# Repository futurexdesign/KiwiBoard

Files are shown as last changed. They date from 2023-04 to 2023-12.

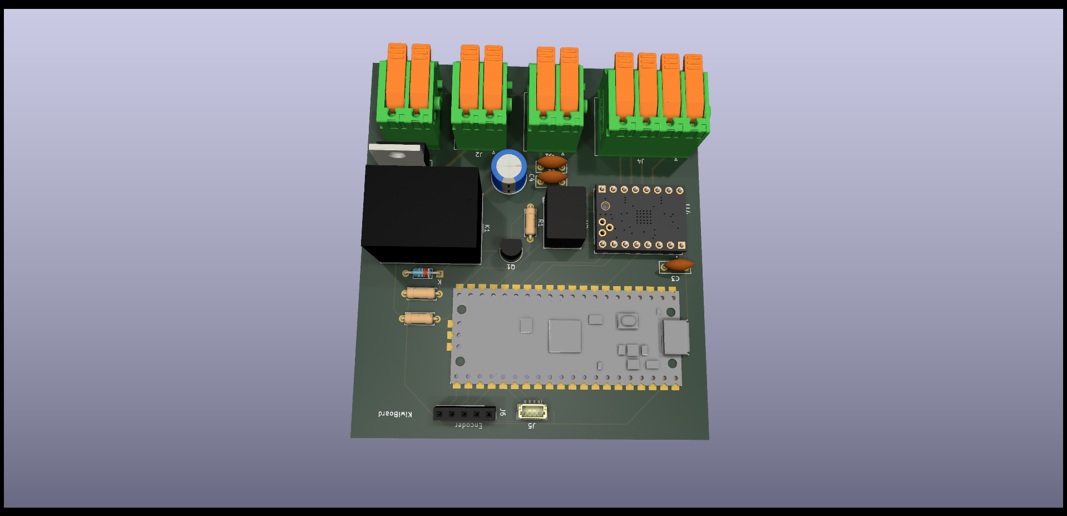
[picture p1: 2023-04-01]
Screenshots/KiwiBoard2.png

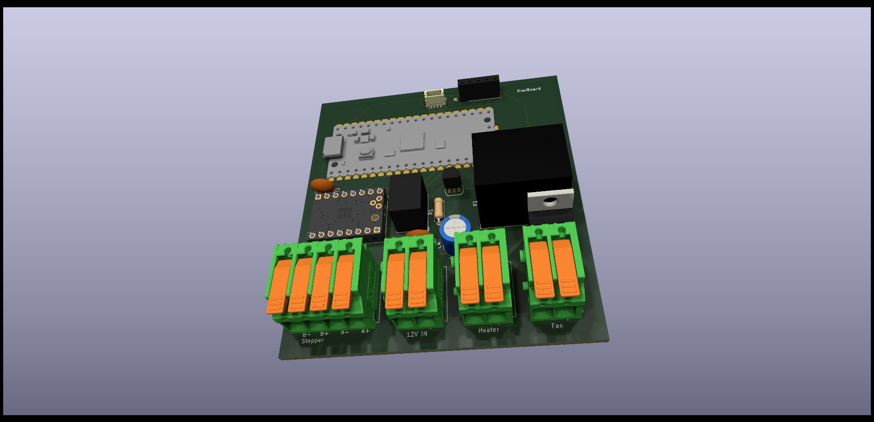
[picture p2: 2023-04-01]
Screenshots/KiwiBoard.png

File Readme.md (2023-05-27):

# Kiwiboard 
Control board for the KiwiCleaner watch cleaning machine.  Intended to provide an all-in-one option for the design. 

## Board Goals
- Have a single PCB with connections for the stepper motor, heater, fan, and user interface for ease of wiring. 
- Integrate a Trinamic silent stepper driver to greatly reduce volume. 
- Simplify the user interface for switching between run-modes. 
- Allow cooling fan to run for a timed period after a dry cycle, to allow the heater to safely cool down. 
- Not cost too much more than the original solution, with the understanding that there is greater functionality. 

## Theory of Operation
- Power input is 12V 
- Input is protected by a resettable PolyFuse with rated 10A constant load capacity.  
- Main Microcontroller is a RaspberryPi Pico (RP2040).  
  - This can be either the normal version, or the "header" version.  Can be mounted either way, board contains both the SMD and THT pads. 
- Display a 240x320 Color TFT LCD Connected via SPI
- User interface is controlled via a rotary encoder with pushbutton
- Pico has full control of stepper via SPI connection to the TMC5160 board. 
   - The Integrated Ramp Generator contained within the TMC5160 is utilized to control all motion, allowing very smooth and precise control over basket motion.  
- Pico can enable / disable the drive output via MOTOR_EN (Active Low)
- Pico can activate the Heater by pulling HEATER_CTL High, switching on the relay (3.3v coil).
- Pico can activate the fan by pulling FAN_CTL high, fan current conducted by the TIP120
- 3.3v power provided by a drop in switching powersupply module for simplicity. 
- All power connectors are Phoenix LPT lever connectors.  These support 12awg - 24awg up to a max of 24A.  Can substitute in SPT or any other phoenix connector with the same 5mm pin spacing

An expansion header has been added to support any additional mods people may want. *Example functionality would be a buzzer module to indicate end of cycle.*  Due to the flexability of the microcontroller, we can expose a ton of functionality on 4 pins.  The following IO is available on the expansion connector. 

- 4 independent GPIO pins for input/output 
- 1 hardware i2c bus (i2c1), and 2 GPIO pins (GPI0 and GPIO1)
- 4 pins with a PIO program assigned to them. 

Additionally the expansion header supplys 3.3V and GND connections.

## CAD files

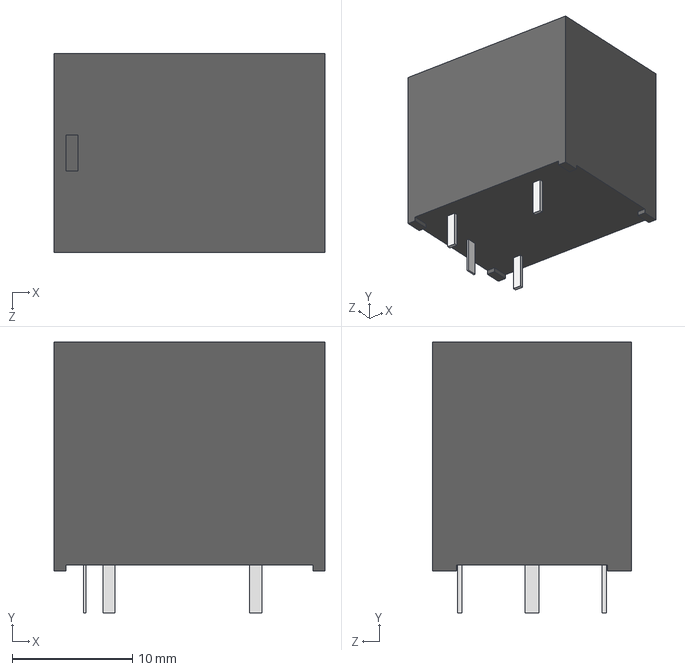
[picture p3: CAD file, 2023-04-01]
project_library/3dmodel/G5LE-1A-EDC5.step
22.5 x 22.5 x 16.5 mm

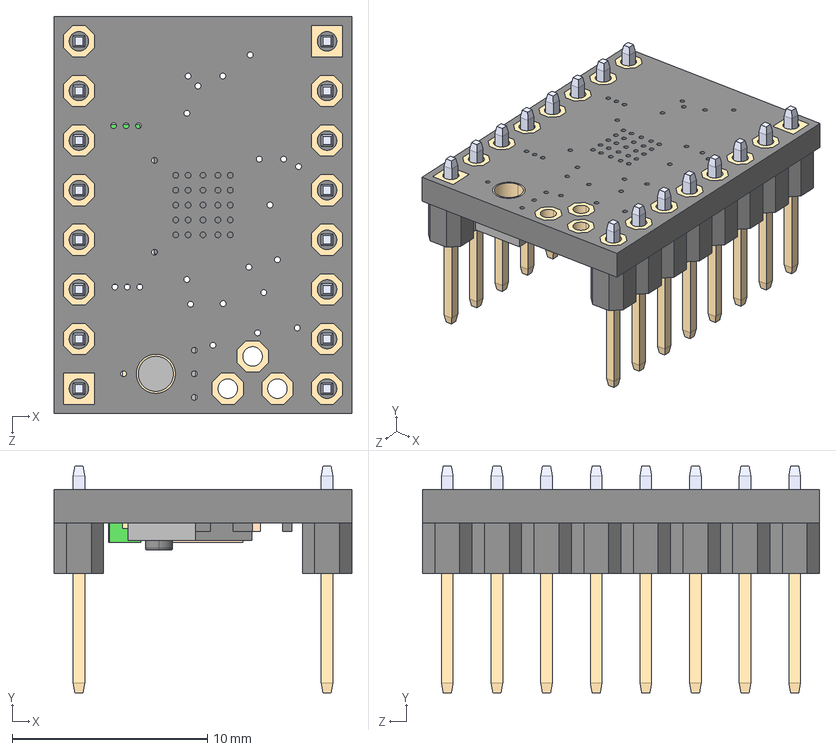
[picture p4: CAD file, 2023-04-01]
project_library/3dmodel/TMC2208_SILENTSTEPSTICK.step
15.2 x 11.6 x 20.3 mm

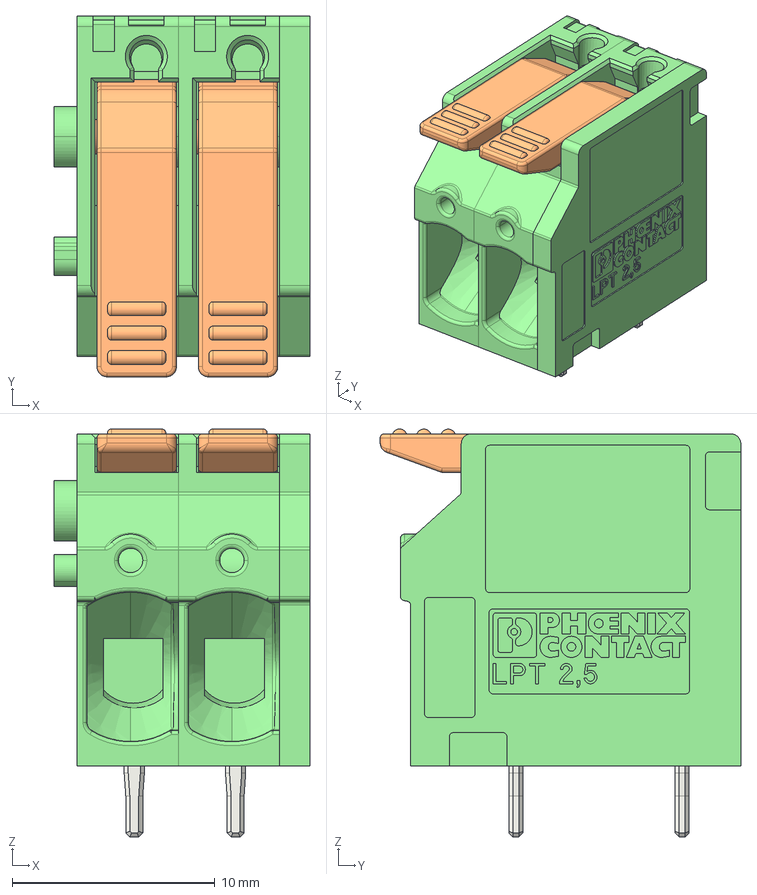
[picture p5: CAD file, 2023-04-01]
project_library/3dmodel/pxc_1190297_02_LPT-2-5-2-5-0_3D.stp
12.6 x 17.8 x 20.1 mm
LP_LPT_2_5_3_50.2.2 x 4
AC_LPT_2_5_LEVER x 2
PK_LPT_2_5_5_00 x 2
DK_LPT_2_5_5_00

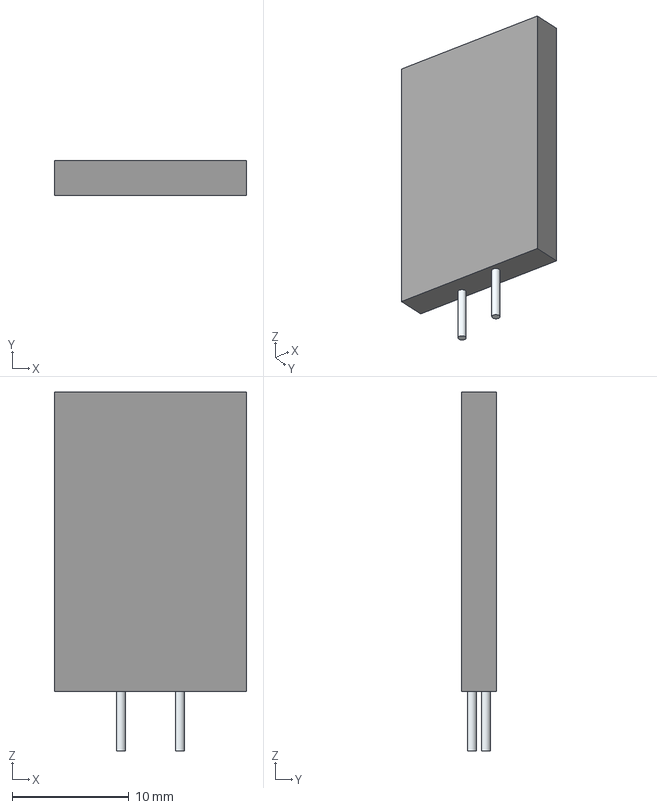
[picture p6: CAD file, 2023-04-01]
project_library/3dmodel/AGRF1000.stp
16.5 x 3.00 x 30.8 mm
Leads

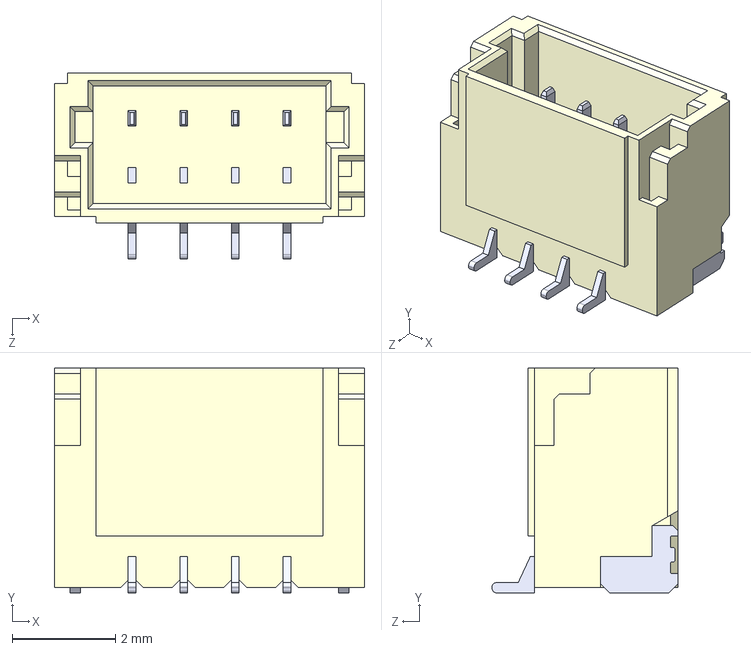
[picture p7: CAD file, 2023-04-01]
project_library/3dmodel/BM04B-SRSS-TBT_LF__SN_.step
6.00 x 4.35 x 3.60 mm

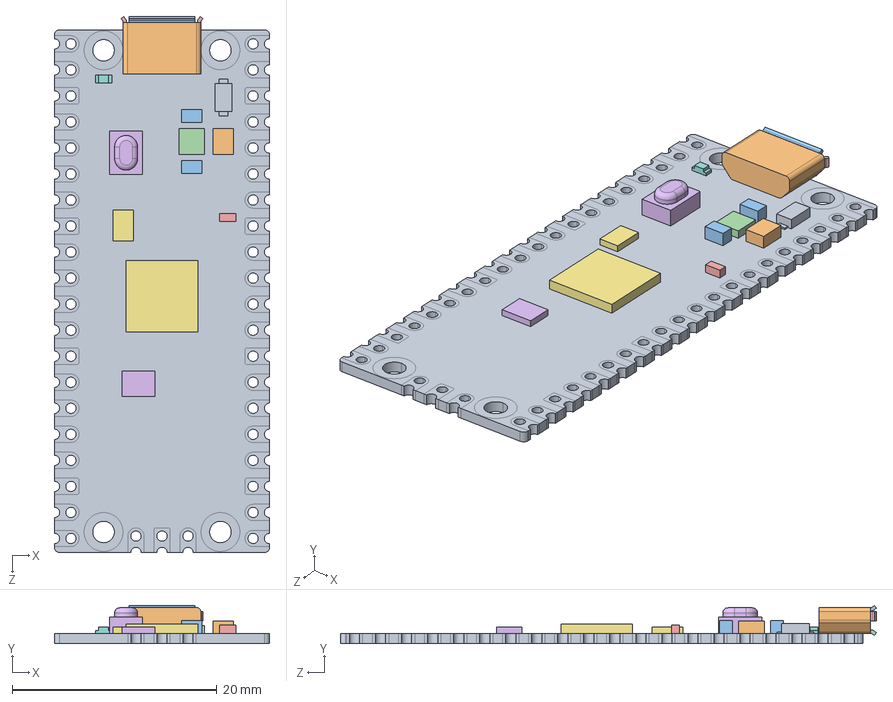
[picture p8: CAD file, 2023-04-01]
project_library/3dmodel/Pico-R3.step
21.0 x 3.73 x 52.3 mm
PICO_REF_BOARD.STEP
PICO_REF_USB.STEP
PICO_REF_SWITCH.STEP
PICO_REF_MICROCONTROLLER.STEP
PICO_REF_LED.STEP
PICO_REF_ONSEMI.STEP
PICO_BOURNS.STEP
PICO_MURATA.STEP x 2
PICO_RICHTEK.STEP
PICO_DIODES.STEP
PICO_AEL.STEP
PICO_WINBOND.STEP

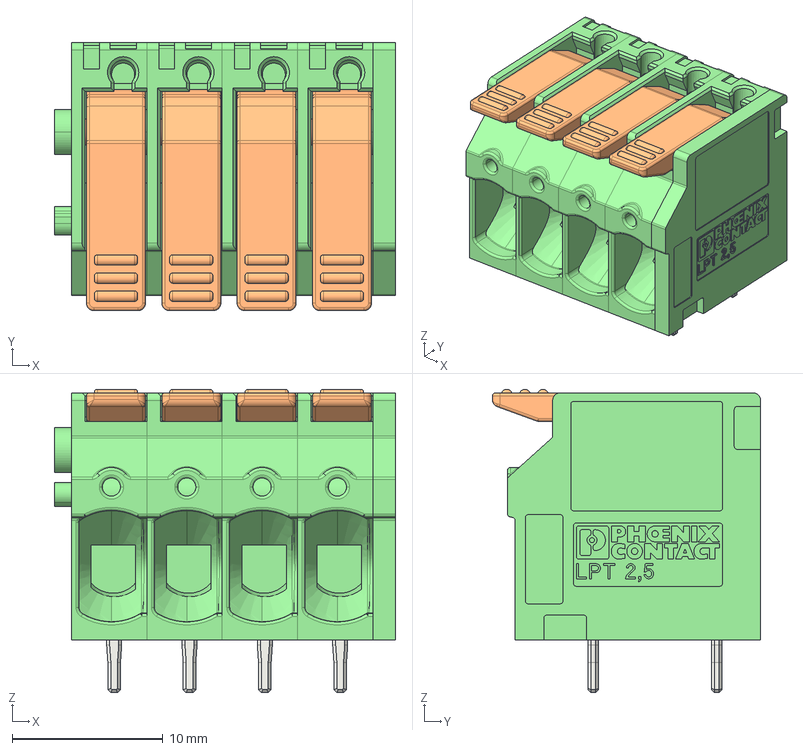
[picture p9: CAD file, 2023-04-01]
project_library/3dmodel/pxc_1190299_02_LPT-2-5-4-5-0_3D.stp
22.6 x 17.8 x 20.1 mm
LP_LPT_2_5_3_50.4 x 8
PK_LPT_2_5_5_00.2 x 4
AC_LPT_2_5_LEVER.2 x 4
DK_LPT_2_5_5_00

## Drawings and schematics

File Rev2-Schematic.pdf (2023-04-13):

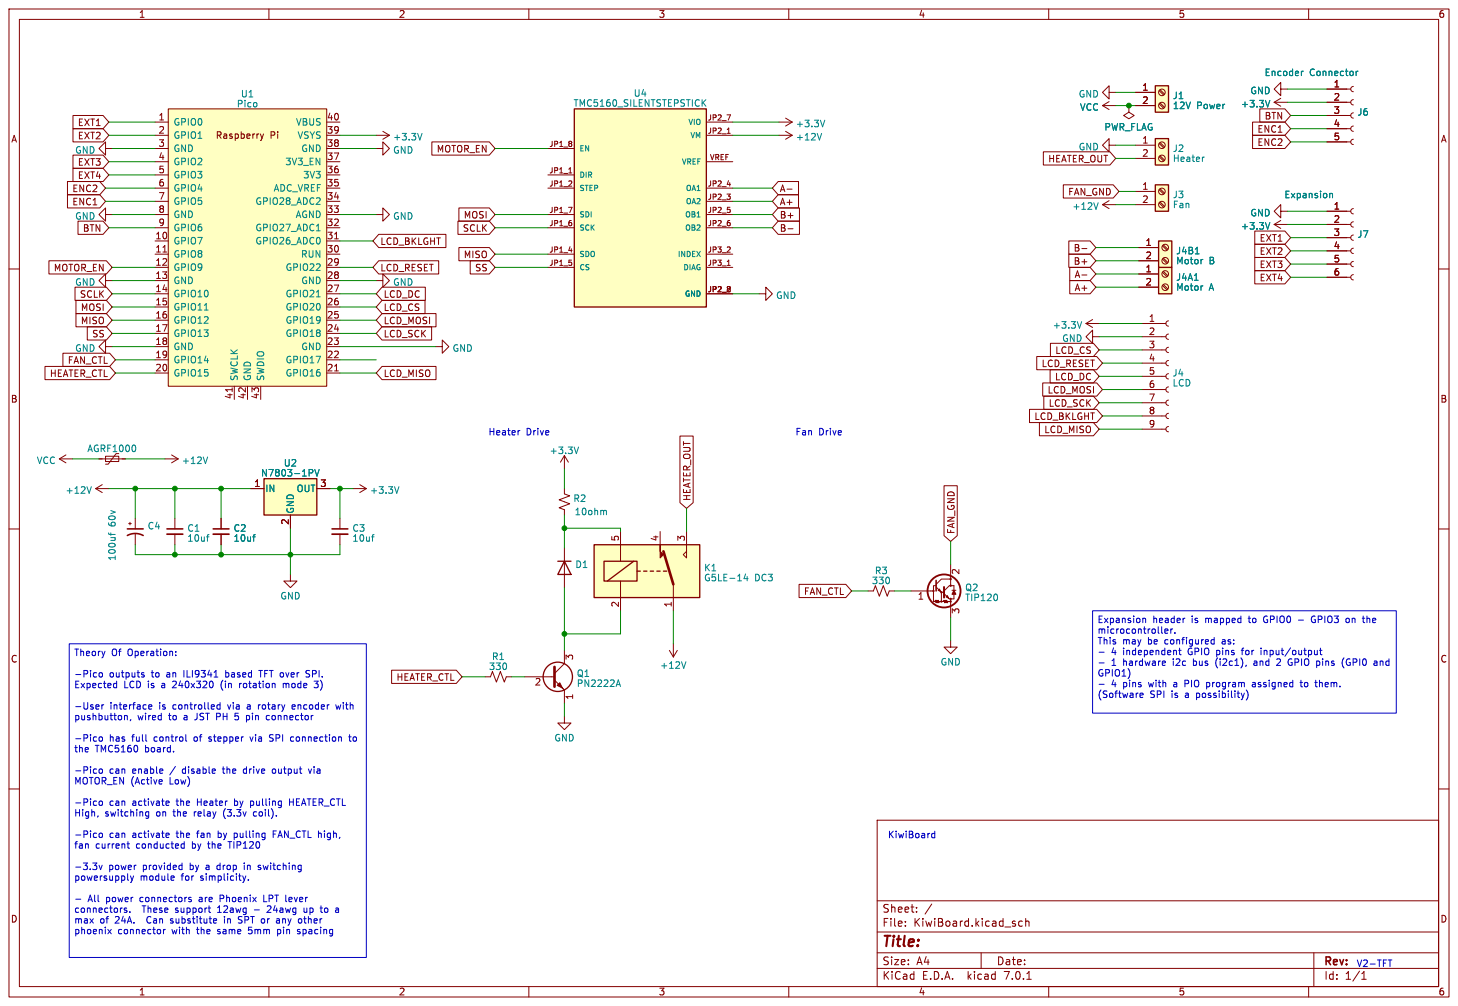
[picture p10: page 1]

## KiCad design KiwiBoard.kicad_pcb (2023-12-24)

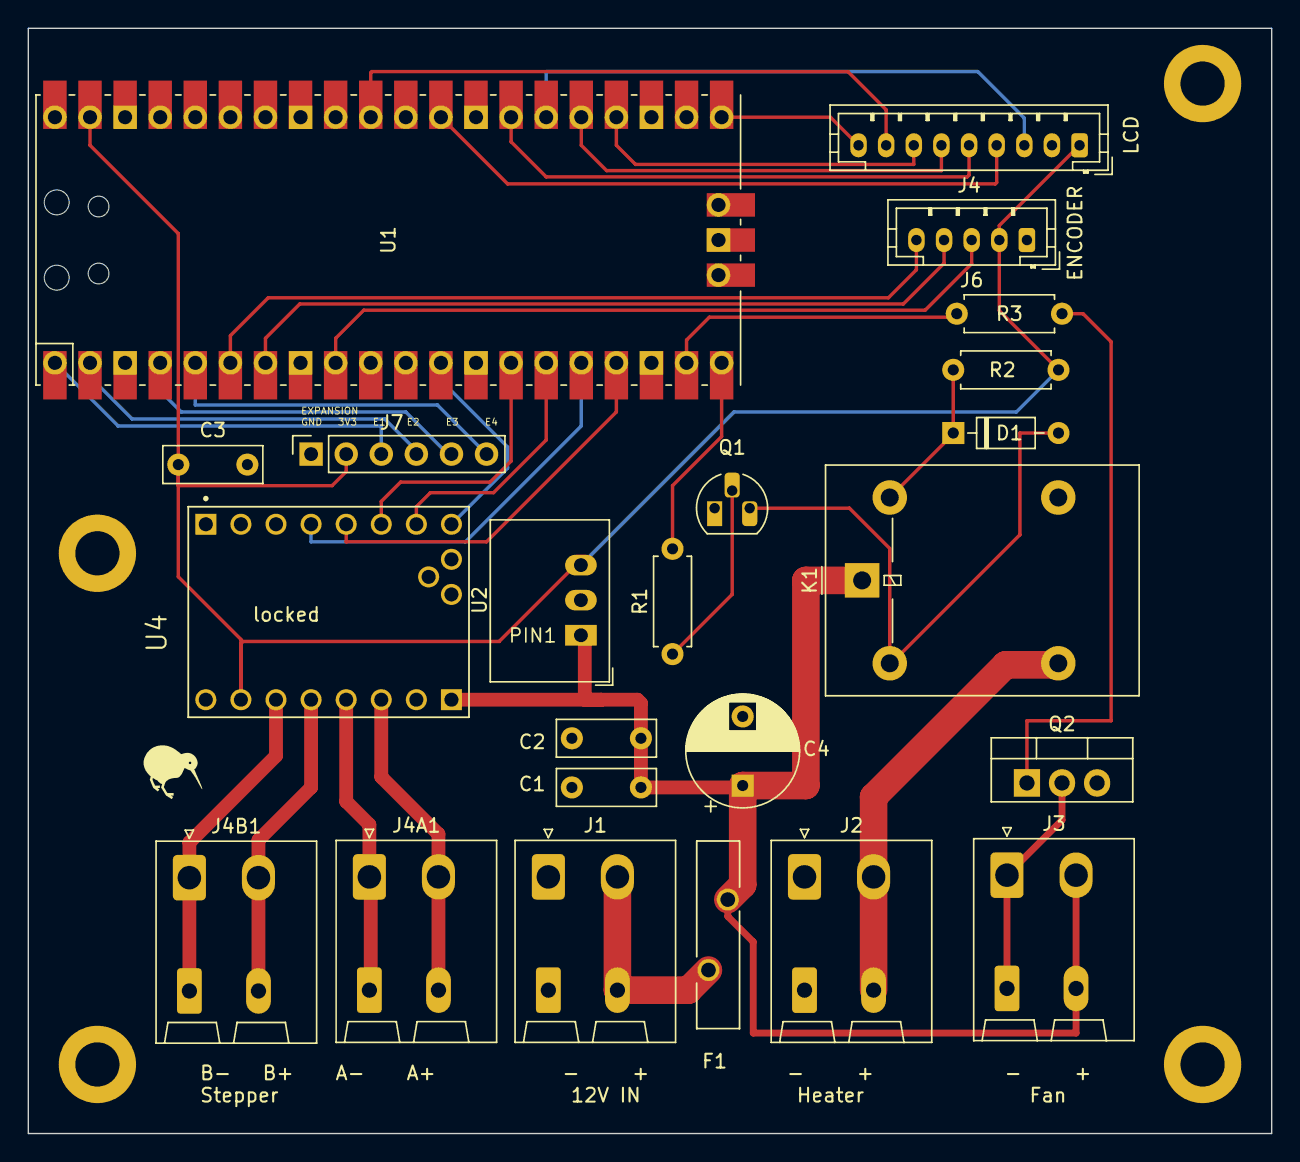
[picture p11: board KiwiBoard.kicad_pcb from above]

Board: 2 copper layers, 90.0 x 80.0 mm, 23 parts (0 on the bottom side), 35 nets.

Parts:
C1, C2, C3: 10uf; C_Disc_D7.0mm_W2.5mm_P5.00mm
C4: 100uf 60v; CP_Radial_D8.0mm_P5.00mm
D1: 1N4148; D_DO-35_SOD27_P7.62mm_Horizontal
F1: AGRF1000; FUSRB510W81L1358T310H1980
J1: 12V Power; Kiwiboard - PhoenixContact_SPT_2.5_2-H-5.0-EX_1x02_P5.0mm_H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
J2: Heater; Kiwiboard - PhoenixContact_SPT_2.5_2-H-5.0-EX_1x02_P5.0mm_H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
J3: Fan; Kiwiboard - PhoenixContact_SPT_2.5_2-H-5.0-EX_1x02_P5.0mm_H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
J4: LCD; JST_PH_B9B-PH-K_1x09_P2.00mm_Vertical
J4A1: Motor A; Kiwiboard - PhoenixContact_SPT_2.5_2-H-5.0-EX_1x02_P5.0mm_H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
J4B1: Motor B; Kiwiboard - PhoenixContact_SPT_2.5_2-H-5.0-EX_1x02_P5.0mm_H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
J6: Encoder Connector; JST_PH_B5B-PH-K_1x05_P2.00mm_Vertical
J7: Expansion; PinSocket_1x06_P2.54mm_Vertical
K1: G5LE-14 DC3; Relay_SPDT_Omron-G5LE-1
Q1: PN2222A; TO-92_HandSolder
Q2: TIP120; TO-220-3_Vertical
R1, R3: 330; R_Axial_DIN0207_L6.3mm_D2.5mm_P7.62mm_Horizontal
R2: 10OHM-1/10W-5%; R_Axial_DIN0207_L6.3mm_D2.5mm_P7.62mm_Horizontal
U1: Pico; RPi_Pico_SMD_TH
U2: N7803-1PV; Converter_DCDC_RECOM_R-78E-0.5_THT
U4: TMC5160_SILENTSTEPSTICK; MODULE_TMC2208_SILENTSTEPSTICK

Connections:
+3.3V: C3.1, J4.1, J6.2, J7.2, R2.1, U1.39 (VSYS), U2.3 (OUT), U4.JP2_7 (VIO)
+12V: C1.1, C2.1, C4.1, F1.2, J3.2, K1.1, U2.1 (IN), U4.JP2_1 (VM)
A+: J4A1.2, U4.JP2_3 (OA2)
A-: J4A1.1, U4.JP2_4 (OA1)
B+: J4B1.2, U4.JP2_5 (OB1)
B-: J4B1.1, U4.JP2_6 (OB2)
BTN: J6.3, U1.9 (GPIO6)
ENC1: J6.4, U1.7 (GPIO5)
ENC2: J6.5, U1.6 (GPIO4)
EXT1: J7.3, U1.1 (GPIO0)
EXT2: J7.4, U1.2 (GPIO1)
EXT3: J7.5, U1.4 (GPIO2)
EXT4: J7.6, U1.5 (GPIO3)
FAN_CTL: R3.2, U1.19 (GPIO14)
FAN_GND: J3.1, Q2.2 (C)
GND: C1.2, C2.2, C3.2, C4.2, J1.1, J2.1, J4.2, J6.1, J7.1, Q1.1 (E), Q2.3 (E), U1.3 (GND), U1.8 (GND), U1.13 (GND), U1.18 (GND), U1.23 (GND), U1.28 (GND), U1.33 (AGND), U1.38 (GND), U2.2 (GND), U4.JP2_2 (GND), U4.JP2_8 (GND)
HEATER_CTL: R1.2, U1.20 (GPIO15)
HEATER_OUT: J2.2, K1.3
LCD_BKLGHT: J4.8, U1.31 (GPIO26_ADC0)
LCD_CS: J4.3, U1.26 (GPIO20)
LCD_DC: J4.5, U1.27 (GPIO21)
LCD_MISO: J4.9, U1.21 (GPIO16)
LCD_MOSI: J4.6, U1.25 (GPIO19)
LCD_RESET: J4.4, U1.29 (GPIO22)
LCD_SCK: J4.7, U1.24 (GPIO18)
MISO: U1.16 (GPIO12), U4.JP1_4 (SDO)
MOSI: U1.15 (GPIO11), U4.JP1_7 (SDI)
MOTOR_EN: U1.12 (GPIO9), U4.JP1_8 (EN)
unnamed: D1.2 (A), K1.2, Q1.3 (C)
unnamed: D1.1 (K), K1.5, R2.2
unnamed: Q1.2 (B), R1.1
unnamed: Q2.1 (B), R3.1
SCLK: U1.14 (GPIO10), U4.JP1_6 (SCK)
SS: U1.17 (GPIO13), U4.JP1_5 (CS)
VCC: F1.1, J1.2

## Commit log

2023-04-04 Mechanical layout with original connectors
    [KiwiBoard-bom.csv, KiwiBoard.kicad_pcb]
2023-04-06 Change to JST PH connectors for OLED and Encoder. Adjust spacing for the 3v3 regulator
    [KiwiBoard.kicad_pcb, KiwiBoard.kicad_sch]
2023-04-07 Change to 2p connectors for the motor. Retaining the ability to use the 2row connectors or one row connectors
    [KiwiBoard-B_Cu.gbr, KiwiBoard-B_Mask.gbr, KiwiBoard-B_Silkscreen.gbr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]
2023-04-09 reworked with JST PH connectors, move raspi to board edge
    [KiwiBoard-B_Cu.gbr, KiwiBoard-B_Mask.gbr, KiwiBoard-B_Silkscreen.gbr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]
2023-04-11 Rev2 board, LCD connector, adjusted Q1 footprint. Pico slid to edge
    [KiwiBoard.kicad_pcb, KiwiBoard.kicad_sch]
2023-12-24 resize upper row of holes, add a bird
    [KiwiBoard.kicad_pcb]
